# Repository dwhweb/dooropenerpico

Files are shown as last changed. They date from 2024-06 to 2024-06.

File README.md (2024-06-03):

Chicken 

# dooropenerpico

## Project overview

The purpose of this project is to create a door opener which can open and close the door to a chicken coop. It consists of —

- Python code written to run on a Raspberry Pi Pico W (hereafter referred to as the Pico).
- Various OpenSCAD models which can be customised and exported to .stl files for 3D printing.

The door can be toggled by pressing a button, and is integrated with Home Assistant as an MQTT entity and as such can be automated (for example, to open at sunrise). The microcontroller can also be optionally started with a web server for setup and debugging purposes by holding the button at startup.

On startup, the microcontroller will attempt to establish a connection to the wireless SSID specified within `/lib/dooropenerpico/credentials.conf`, then attempt to connect to the MQTT server also specified within that file. The onboard LED will blink to notify that this is happening, and will go solid when a connection is established. Following this, the green and red LEDs on the control panel will light in an alternating fashion twice to signify the board has successfully started. Most functions and actions the board takes are logged to the console for easy debugging in Thonny or your IDE of choice.

The door opener can operate without network functionality (button actuation only) by simply omitting `credentials.conf` if required.

## Documentation

Extensive documentation detailing how to build this project can be found [here](https://dwhweb.github.io/dooropenerpico).

## Licensing and acknowledgements

Unless otherwise noted for constituent parts, this project is shared under the terms of of the [CC-BY-4.0](https://creativecommons.org/licenses/by/4.0/) licence. Please attribute **dwhweb** in any derivative works.



The wiring diagram incorporates an .svg of the pinout of the Pico, which is the property of Raspberry Pi Ltd and is licenced under the terms of the [CC-BY-SA 4.0](https://creativecommons.org/licenses/by-sa/4.0/) licence, consequently the diagram is also shared under the terms of this licence.

The dooropenerpico project incorporates the following software, libraries and resources. If I've somehow missed you out, please get in touch —

- [Chicken image by Vecteezy](https://www.vecteezy.com/vector-art/6046486-chicken-logo-cartoon-character-cute-cartoon-rooster-chicken-gives-thumbs-up-vector-logo-illustrationt) (modified)
- The [Microdot](https://github.com/miguelgrinberg/microdot) library
- The [Picozero](https://github.com/RaspberryPiFoundation/picozero) library
- The [Public Domain Involute Parameterized Gears](https://www.thingiverse.com/thing:5505) library (modified to fix some minor issues)
- The [Umqtt.robust2](https://github.com/fizista/micropython-umqtt.robust2) library

The following software, libraries or resources were also used when creating this project —

- The [Belfry OpenSCAD library v2](https://github.com/BelfrySCAD/BOSL2)
- The [Furo theme](https://github.com/pradyunsg/furo)
- [Git](https://git-scm.com/)
- [Home Assistant](https://www.home-assistant.io/)
- [LunarVim](https://www.lunarvim.org/)
- [MicroPython](https://micropython.org/)
- [Mosquitto MQTT broker](https://mosquitto.org/)
- [MQTT Explorer](https://mqtt-explorer.com/)
- [OpenSCAD](https://openscad.org/)
- [PrusaSlicer](https://www.prusa3d.com/en/page/prusaslicer_424/)
- [Python](https://www.python.org/)
- [Rshell](https://github.com/dhylands/rshell)
- [Sphinx](https://www.sphinx-doc.org/en/master/)
- [Thonny](https://thonny.org/)
- The [Watchdog](https://github.com/gorakhargosh/watchdog) library

Thanks to the wider open source community for making projects like this possible and for creating fantastic things that we use every day.

## Contacts

Errors and omissions are likely and there are undoubtedly aspects of the project which are obvious to me but need clarification and improvement. You can contact me via email regarding this project at **dooropenerpico at dwhweb dot org**, or in the case of bugs raise a [Github issue](https://github.com/dwhweb/dooropenerpico/issues).

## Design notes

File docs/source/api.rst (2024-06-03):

API documentation
=================

.. toctree::

   class_structure

.. autosummary::
   :toctree: generated

   dooropenerpico.conf.Conf
   dooropenerpico.dooropenerpico.DoorOpenerPico
   dooropenerpico.dooropenerpicobase.DoorOpenerPicoBase
   dooropenerpico.dooropenerpiconetwork.DoorOpenerPicoNetwork
   dooropenerpico.dooropenerpicoweb.DoorOpenerPicoWeb
   dooropenerpico.print_debug.Print_debug

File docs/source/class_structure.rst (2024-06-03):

Class structure overview
========================

``main.py`` initially creates an instance of :class:`~dooropenerpico.dooropenerpico.DoorOpenerPico` which then instantiates one of three types of instance —

* :class:`~dooropenerpico.dooropenerpicobase.DoorOpenerPicoBase` (button functionality only) if ``credentials.conf`` (login credentials) or ``discovery.conf`` (Home Assistant discovery payload) can't be found.
* :class:`~dooropenerpico.dooropenerpicoweb.DoorOpenerPicoWeb` (web server) if the control panel button is held on startup.
* :class:`~dooropenerpico.dooropenerpiconetwork.DoorOpenerPicoNetwork` (Home Assistant/MQTT) otherwise.

These three classes have an inheritance relationship in terms of progressive enhancement as such —

.. inheritance-diagram:: dooropenerpico.dooropenerpicoweb
   :parts: 1

i.e. The majority of base functionality is implemented in :class:`~dooropenerpico.dooropenerpicobase.DoorOpenerPicoBase`, :class:`~dooropenerpico.dooropenerpiconetwork.DoorOpenerPicoNetwork` inherits from that and implements network/MQTT functionality, and :class:`~dooropenerpico.dooropenerpicoweb.DoorOpenerPicoWeb` inherits from that and implements web server functionality.

Aside from this, there are two utility classes —

* :class:`~dooropenerpico.conf.Conf` which is used to retrieve and validate ``.conf`` files.
* :class:`~dooropenerpico.print_debug.Print_debug` which is used to print debug messages to the console with an optional timestamp.

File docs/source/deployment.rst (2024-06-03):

.. include:: global.rst

Deployment and setup
====================

Cloning the repository
----------------------
Initially, clone the repository using Git —

.. code:: bash

   git clone https://www.github.com/dwhweb/dooropenerpico.git

Creating MQTT credentials
-------------------------
Assuming you plan on using the Home Assistant/MQTT broker functionality you'll need to create new user login credentials for the Pi Pico to use. You can find this option on Home Assistant in Settings → People → Users (Add user button) i.e. 

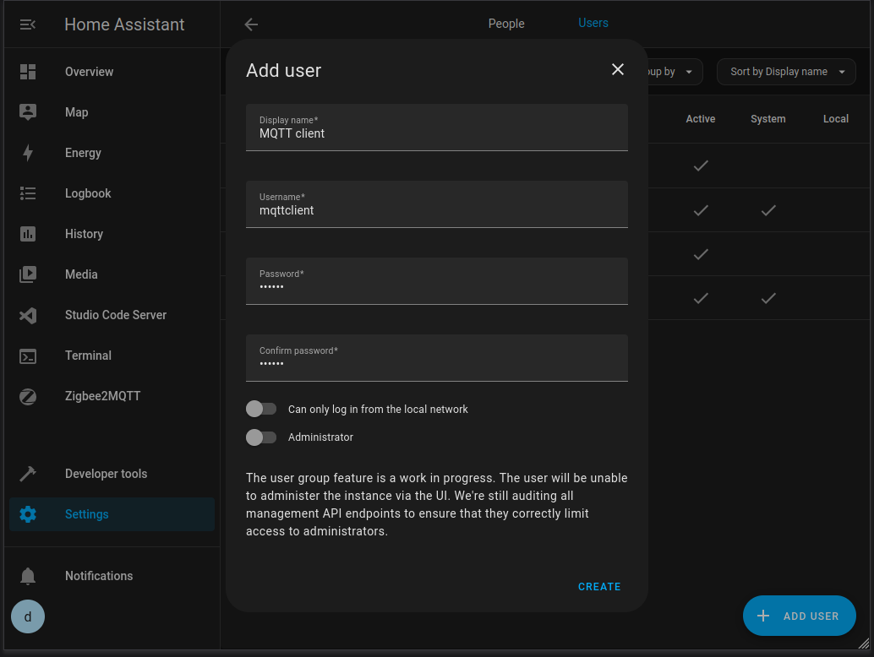
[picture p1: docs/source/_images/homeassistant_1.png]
Home Assistant users dialog


Once you've done that, you might want to verify that you can connect to the broker using MQTT explorer.
 
Deploying code to the Pi Pico
-----------------------------
Before you can copy the code across, you'll need to copy the MicroPython firmware to the Pico, follow the instructions on the `Raspberry Pi website. <https://www.raspberrypi.com/documentation/microcontrollers/micropython.html>`_

Deploying via script
^^^^^^^^^^^^^^^^^^^^
Once you have the MicroPython firmware installed, assuming you're running a \*nix variant you can deploy the code to the Pi Pico using ``deploy.sh`` (you need ``rshell`` for this to run, see the :doc:`software requirements <software>` section).

The script will inform you that the current contents of the Pi Pico will be erased, and ask if you want to set up networking. Assuming this is the case, you will be prompted for —

* Wifi SSID
* Wifi password
* MQTT broker hostname/IP
* MQTT port
* MQTT username
* MQTT password

Otherwise, the credentials file will be deleted and the Pico will operate via button press only (no networking) on boot.

.. note::

   The deployment script takes a little time to copy files across to the Pi Pico and provides little visual feedback while doing so, please be patient!

.. _deploying-manually:

Deploying manually
^^^^^^^^^^^^^^^^^^
If you're running Windows (or just don't want to run the script) and want to deploy the code to the Pi Pico manually, you need to copy ``main.py`` and the ``lib/`` directory across. You can do so using Thonny. With the Pi Pico connected, navigate to the directory where you cloned the code repository, then right click on the file/directory and select "Upload to /" i.e.

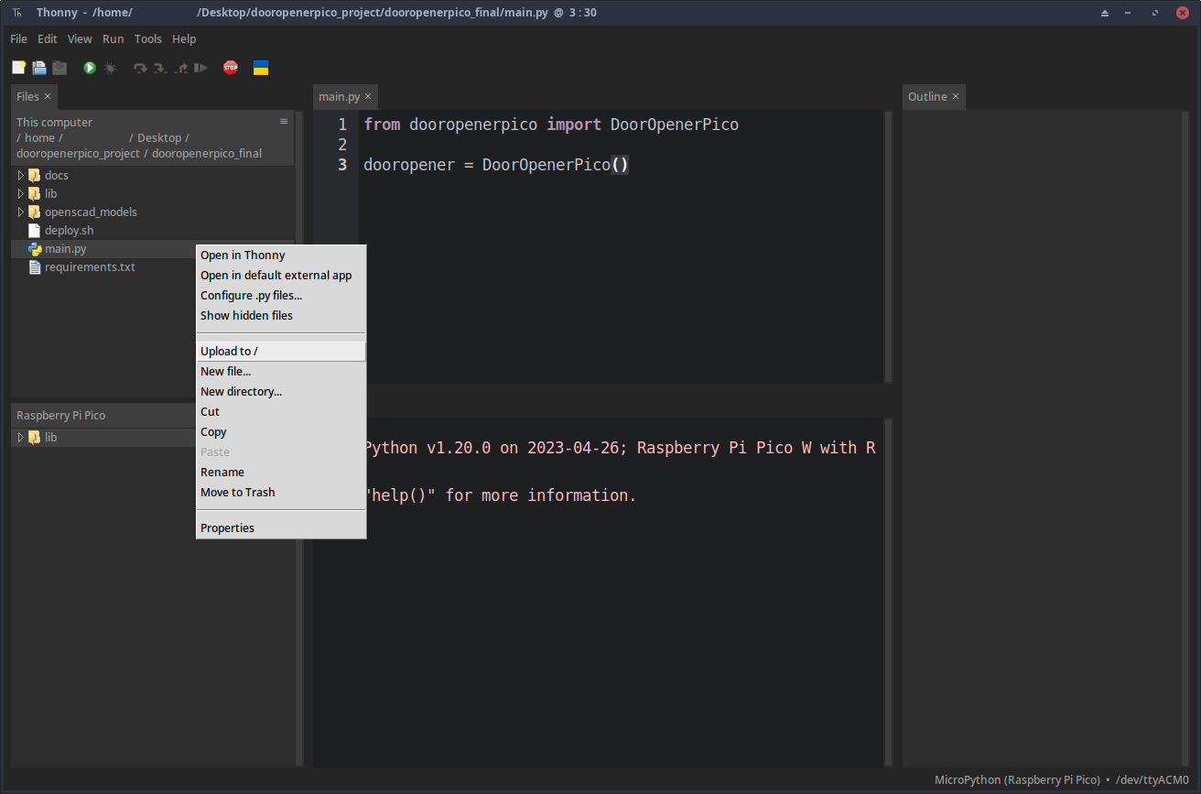
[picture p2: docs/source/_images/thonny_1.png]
Copying files to the Pi Pico


You can alternatively use ``rshell`` to copy the files with —

.. code:: bash

   cp main.py /pyboard/main.py
   cp -r lib/ /pyboard/

Once you've done that, you'll need to edit the credentials file ``/lib/dooropenerpico/credentials.conf`` to add Wifi/MQTT credentials as detailed above, or alternatively just delete the file if you don't plan to use network functionality.

.. _configuration-options:

Configuration options
---------------------

There are a number of configuration options held within ``/lib/dooropenerpico/config.conf`` that you might want to change, these are —

.. list-table::
   :header-rows: 1

   * - Key
     - Notes
   * - ``pulse_time``
     - The length of time the LEDs should pulse to indicate activity, in seconds.
   * - ``led_brightness``
     - Brightness of the LEDs when on, value is a float between 0-1.
   * - ``timeout``
     - The time in seconds after which the door opener aborts an open/close if the door doesn't detect it is in the opposite state, this is a safety feature. The web server provides a feature to time how long actuation takes which is useful in working out an appropriate value, see the :ref:`usage section <time-open-close>`.
   * - ``cushion_open_time``
     - Time after which the door changes speed when opening in seconds, the intention being that you could set the door to open more slowly for the last portion so it opens gently and does not slam. If you don't want this functionality, you can just set ``cushion_open_speed`` to be the same value as ``open_speed``. This must be less than ``timeout``, otherwise the door opener will not start. 
   * - ``cushion_close_time``
     - As above, but for the door closing as opposed to opening.
   * - ``open_speed``
     - The speed at which the door should open between 0 (full speed anti-clockwise) and 1 (full speed clockwise).
   * - ``close_speed``
     - As above, but for closing.
   * - ``cushion_open_speed``
     - The speed at which the door should open for the last (cushion) portion between 0 (full speed anti-clockwise) and 1 (full speed clockwise).
   * - ``cushion_close_speed``
     - As above, but for closing.
   * - ``left_reed_bounce_time``
     - Prevents activation of the left reed switch being detected as multiple events, value is in seconds.
   * - ``right_reed_bounce_time``
     - As above, but for the right reed switch.
   * - ``ping_interval``
     - Interval at which the Pi Pico should attempt to ping the MQTT broker, required to detect connection issues and re-establish connection automatically. If you encounter frequent connection issues it might be worth looking into getting an additional wireless access point or mesh setup.
   * - ``left_speed``
     - Speed at which the servo moves when the user presses the "left" button in the web ui, this is a float value between 0 and 1.
   * - ``right_speed``
     - As above, but for the "right" button.

You're most likely to need to tune the ``timeout`` and cushion times/speeds as it is likely that your coop is a different size than mine and hence the door will take a different amount of time to open or close. 

You'll likely need to tune ``left_speed`` and ``right_speed`` as well, even when using the same servo. There is a trim pot recessed into the side of the servo that you can set with a small phillips head screwdriver, this should be adjusted such that the servo doesn't move when stopped (you can send a stop signal from the web ui, see the :ref:`usage section <web-server>`). 

.. warning::

   Be careful when editing this file as it is validated on boot and if any key is missing or does not have an associated value the Pico won't start.

Setting up Home Assistant
-------------------------

I'm assuming at this point you have the Pico configured such that it successfully connects to both your Wifi and the Home Assistant MQTT broker, you can refer to the :ref:`usage section <console-output>` to see what the console output looks like in Thonny. 

Configuration in Home Assistant at this point should be relatively straightforward and the Pico should show in the list of entities (Settings → Devices & Services → Entities) —

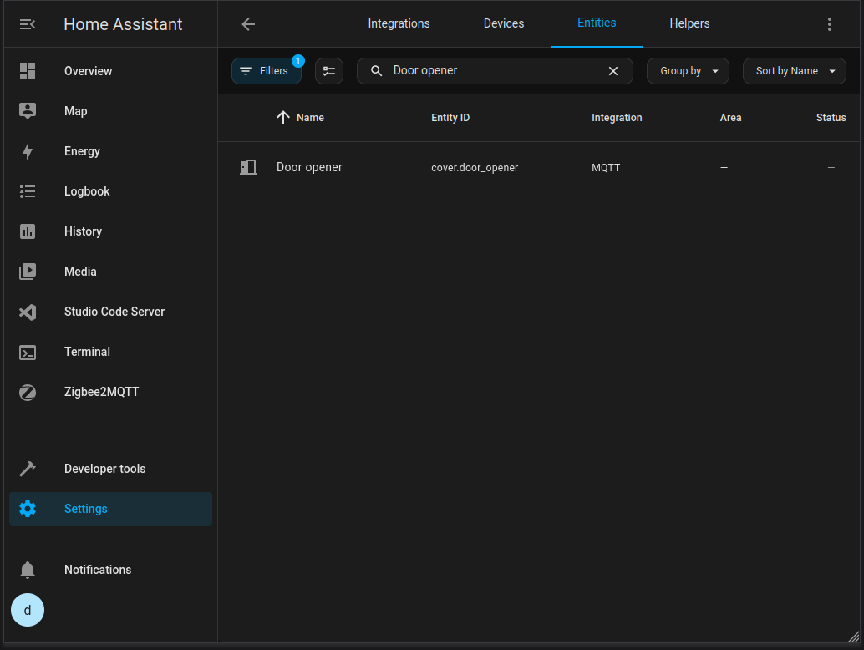
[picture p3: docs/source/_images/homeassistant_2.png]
The door opener entity


You can then add the door opener to the dashboard (Overview → Edit dashboard (pencil) icon → Add card → By entity) —

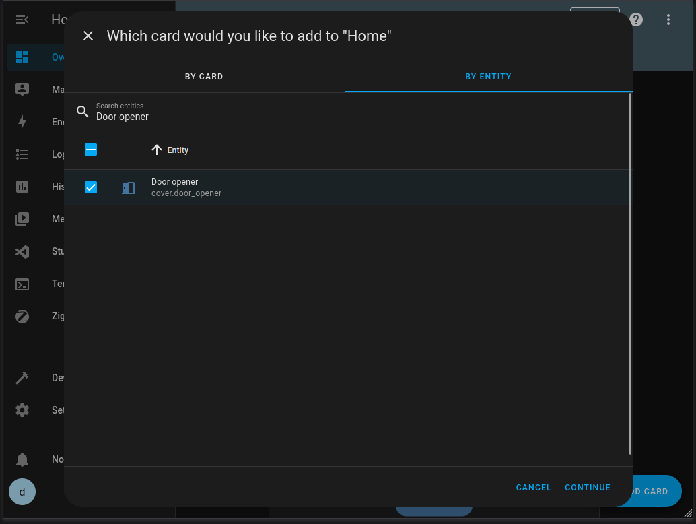
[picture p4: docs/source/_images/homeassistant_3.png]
Adding the door opener to the dashboard


You could then create an automation, for example, to open the door automatically at sunrise (Settings → Automations & scenes → Create automation) —

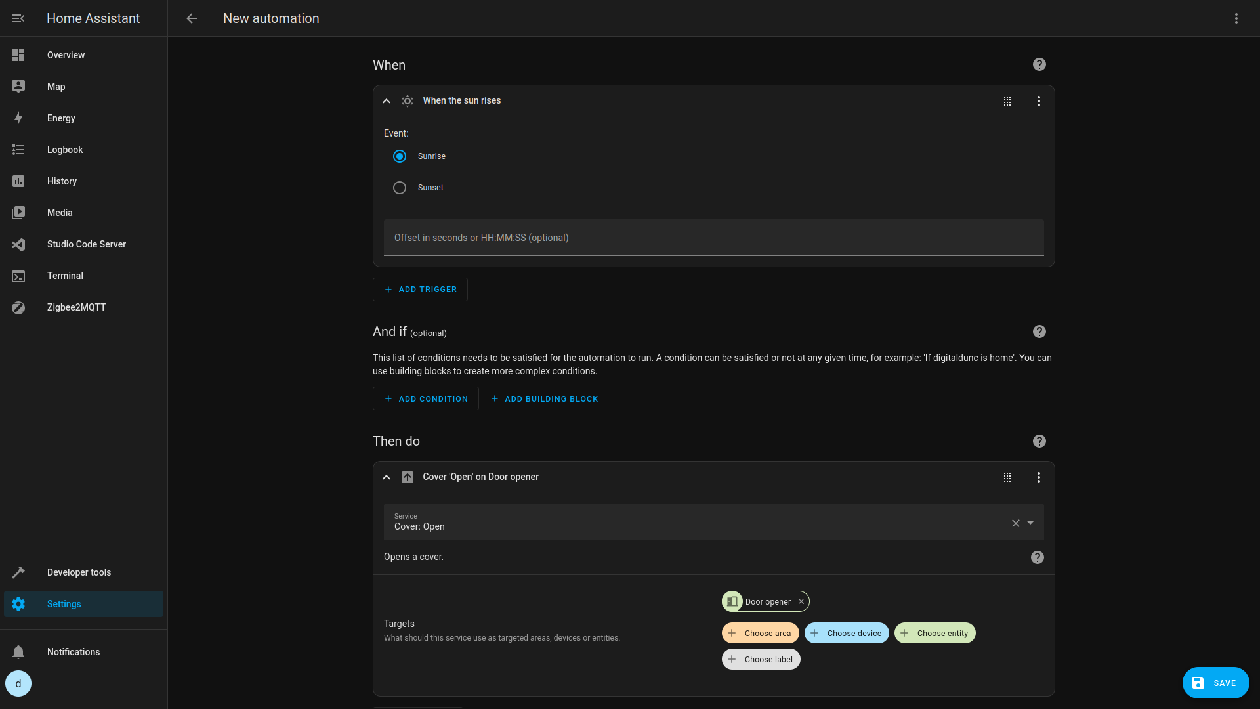
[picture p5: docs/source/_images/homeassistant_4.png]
Door opener automation


I don't personally automate closing the door, as the time at which my chickens decide to go in varies and I don't want them to accidentally get trapped in the door.

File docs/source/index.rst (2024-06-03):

.. include:: global.rst

.. toctree::
   :hidden:
   :maxdepth: 5
   
   Project overview <self>
   video
   skills
   software
   bom
   printing
   wiring
   deployment
   usage
   troubleshooting
   development
   api
   licencing
   contacts

dooropenerpico documentation
============================

Project overview
----------------

The purpose of this project is to create a door opener which can open and close the door to a chicken coop. It consists of —

- Python code written to run on a Raspberry Pi Pico W (hereafter referred to as the Pico).
- Various OpenSCAD models which can be customised and exported to .stl files for 3D printing.

The door can be toggled by pressing a button, and is integrated with `Home Assistant <https://www.home-assistant.io>`_ as an MQTT entity and as such can be automated (for example, to open at sunrise). The microcontroller can also be optionally started with a web server for setup and debugging purposes by holding the button at startup.

On startup, the microcontroller will attempt to establish a connection to the wireless SSID specified within ``/lib/dooropenerpico/credentials.conf``, then attempt to connect to the MQTT server also specified within that file. The onboard LED will blink to notify that this is happening, and will go solid when a connection is established. Following this, the green and red LEDs on the control panel will light in an alternating fashion twice to signify the board has successfully started. Most functions and actions the board takes are logged to the console for easy debugging in Thonny or your IDE of choice.

The door opener can operate without network functionality (button actuation only) by simply omitting ``credentials.conf`` if required.

The files for this project in terms of MicroPython code and OpenSCAD models can be found in the repository on `Github <https://www.github.com/dwhweb/dooropenerpico>`_.

.. note:: 
   I built this project for my own personal use and as such it is likely not suited to your purposes without some minor customisation, but the code and models were created with this in mind and this is covered in more depth in the sections to follow. 

.. tip::
   If you intend on building the project, I suggest you scan the documentation in its entirety before you start so you have a better appreciation of how the various parts (hardware and software) fit together.

.. warning::
   In case it isn't obvious, no warranty is expressed or implied. I am not responsible for any harm that might come to you, your chickens, the fabric of spacetime, etc.

|CC BY 4.0|

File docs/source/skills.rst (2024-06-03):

Required skills
================

I'd suggest that you have the following skills to proceed with this project —

* Familiarity with your operating system of choice, and some technical level of computing experience. 
  
  * Most of the things you'll need to do in the course of building this project can *probably* be done in Windows, but a shell script for code deployment to the Pico is included in the repository so Linux is probably preferable.
  * You'll need some kind of Home Assistance instance to get the most out of this project in terms of automation so familiarity with virtualisation could be beneficial if you want to run it in a VM or container.
* Rudimentary experience of electronics, and the ability to solder. You'll need to wire together some of the components in the BOM (Bill Of Materials).
* Some coding experience in general (especially object-oriented Python) would be beneficial, but coding on your part should be largely unnecessary — important configurables are held within ``.conf`` files.
* Familiarity with OpenSCAD would be beneficial but again, necessary changes on your part should be minimal and important configurables can be changed directly within the OpenSCAD UI.
* 3D printing experience, you should be familiar with standard concepts such as slicing, fill percentages, supports and the properties of different printing materials.

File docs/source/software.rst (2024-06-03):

Software requirements
=====================

I'd suggest the following software if you intend to build this project —

* `Git <https://git-scm.com/>`_ to clone the repository ready for deployment.
* Linux or some flavour of \*nix for running the code deployment Bash script for copying the microcontroller code to the Pi Pico — you can alternatively :ref:`deploy this manually <deploying-manually>`.
* `rshell <https://github.com/dhylands/rshell>`_ if you're using the code deployment script.
* `Thonny <https://thonny.org/>`_ as an IDE — even if you aren't likely to change any of the underlying code the console is invaluable for debugging purposes and Thonny also sets the RTC of the Pico on connection so you can determine *when* an issue happened.
* `OpenSCAD <https://openscad.org/>`_ for customising and exporting the 3D models ready for printing.
* `The Belfry OpenSCAD library v2 <https://github.com/BelfrySCAD/BOSL2>`_ is a required library for the 3D models.
* `PrusaSlicer <https://www.prusa3d.com/en/page/prusaslicer_424/>`_ is my preferred slicer, but Cura or similar would work just as well.
* `Home Assistant <https://www.home-assistant.io/>`_ for automating when the door opens or closes, if you don't care about network functionality and just want to use the switch you can omit this.
* `Mosquitto MQTT broker <https://mosquitto.org/>`_ installed as a Home Assistant add-on, you may already have this depending on what is running on your Home Assistant instance.
* `MQTT Explorer <https://mqtt-explorer.com/>`_ is useful for debugging MQTT issues.

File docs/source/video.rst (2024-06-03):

Video and images
================

Video
-----
Video of the door opener actuating —

..  youtube:: s7rDaMlY8wI

Fully assembled
---------------
The opener looks like this when assembled —

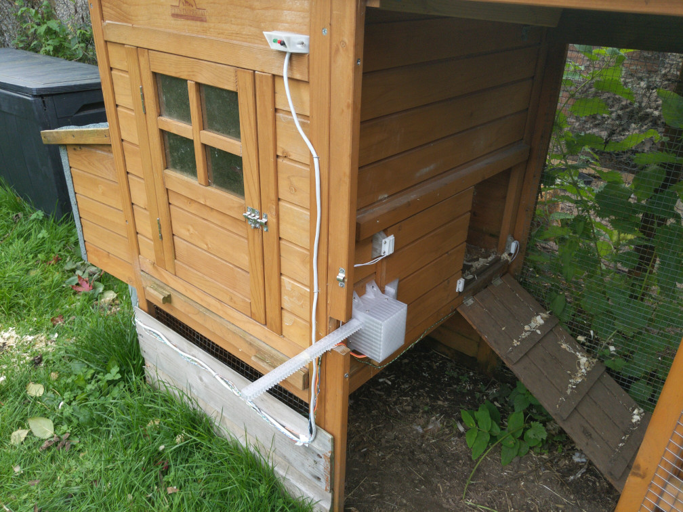
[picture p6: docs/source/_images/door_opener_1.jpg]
Assembled door opener


Pico case
---------
The casing for the Pico is out of shot in a plastic box underneath the coop which also holds a mains supply. The case for the Pico without the cover looks like this —

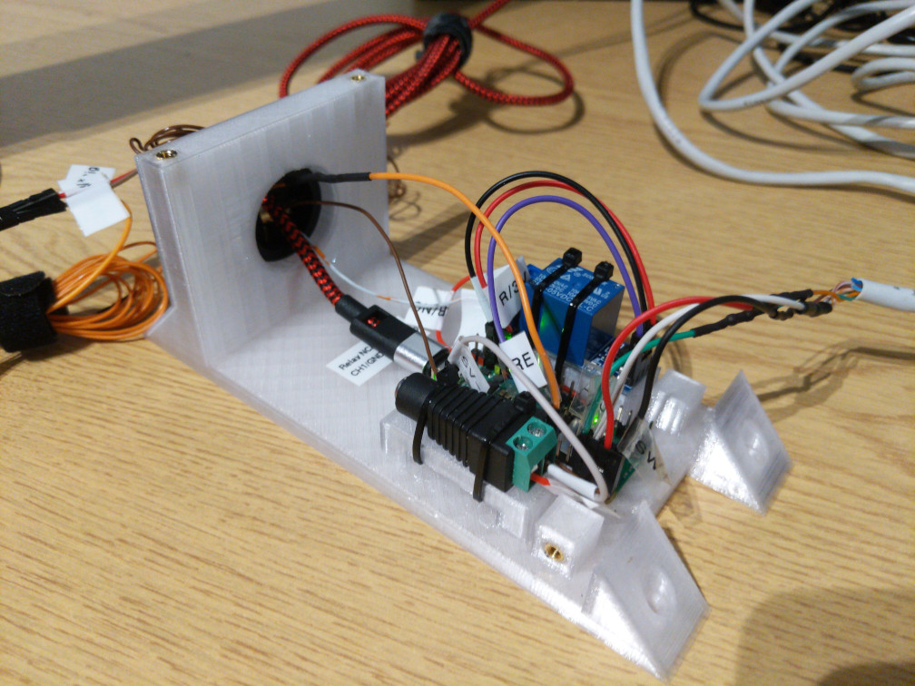
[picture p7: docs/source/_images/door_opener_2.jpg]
Pi pico case without cover


Note that the project is only partially assembled in the above picture and not all cables are shown. Fully assembled, the case looks like this —

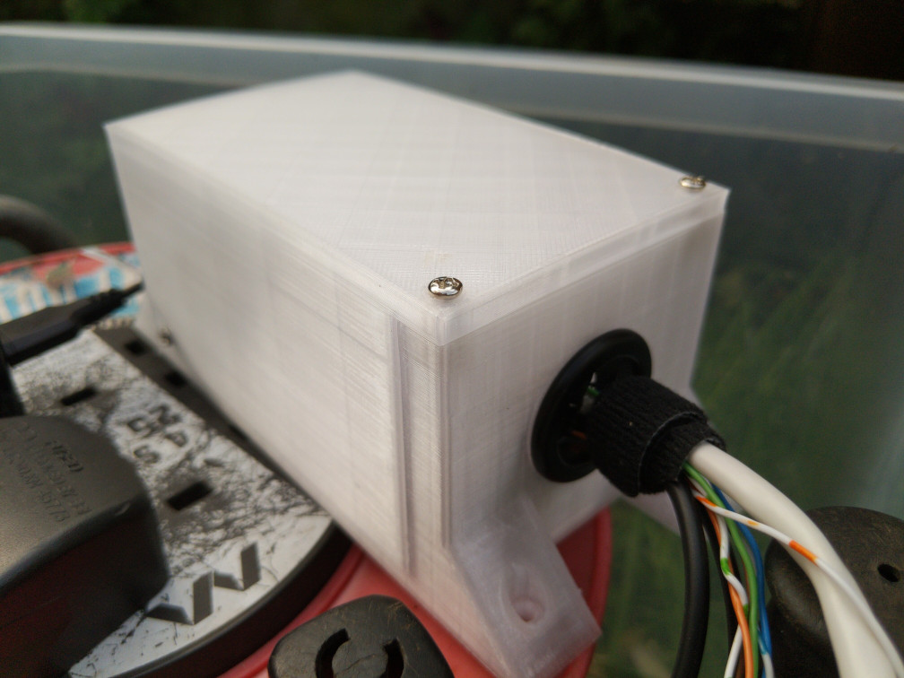
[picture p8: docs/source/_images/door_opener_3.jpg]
Pi pico case with cover


Control panel
-------------
The control panel looks like this —

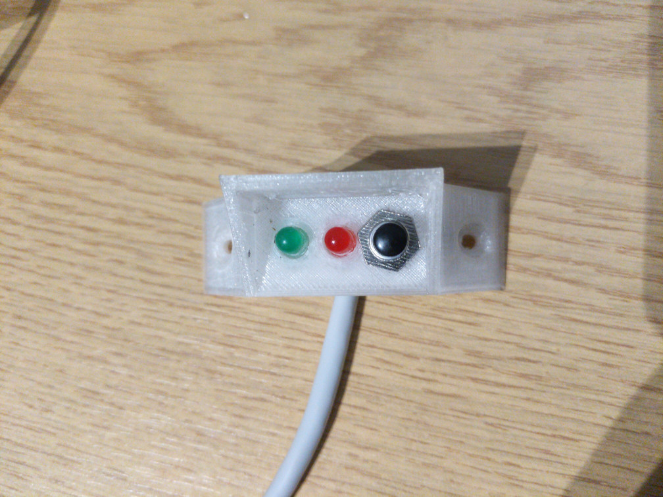
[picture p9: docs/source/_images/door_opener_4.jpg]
Control panel


Reed switch mounts
------------------
Left and right reed switch mounts (respectively) look like this —

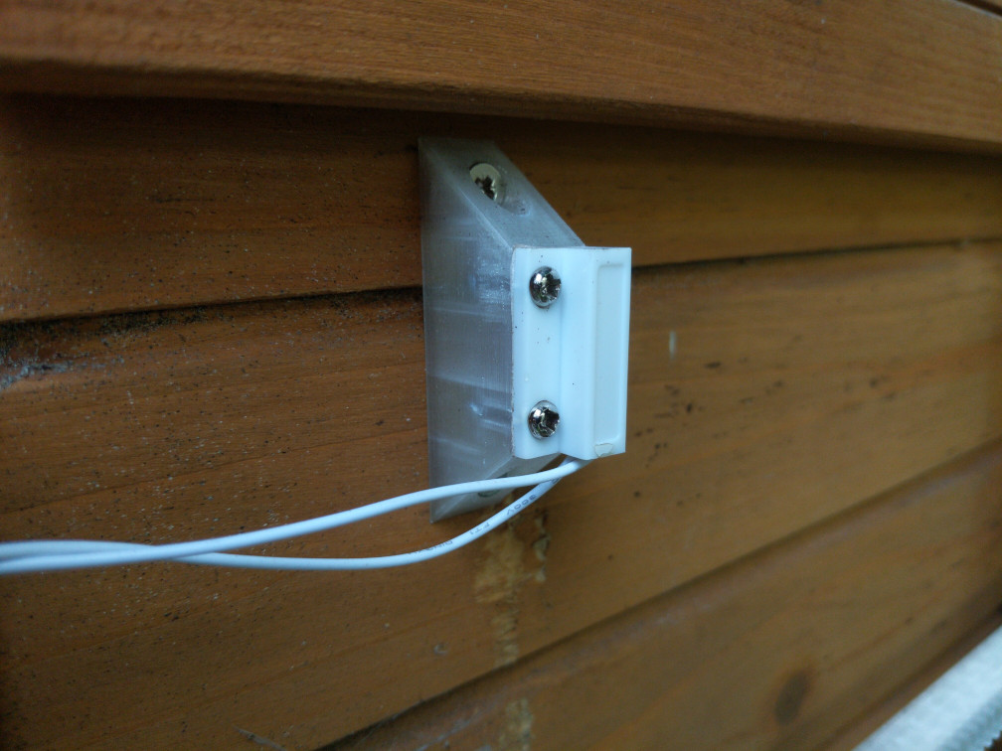
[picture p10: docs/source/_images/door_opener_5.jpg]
Left reed switch mount


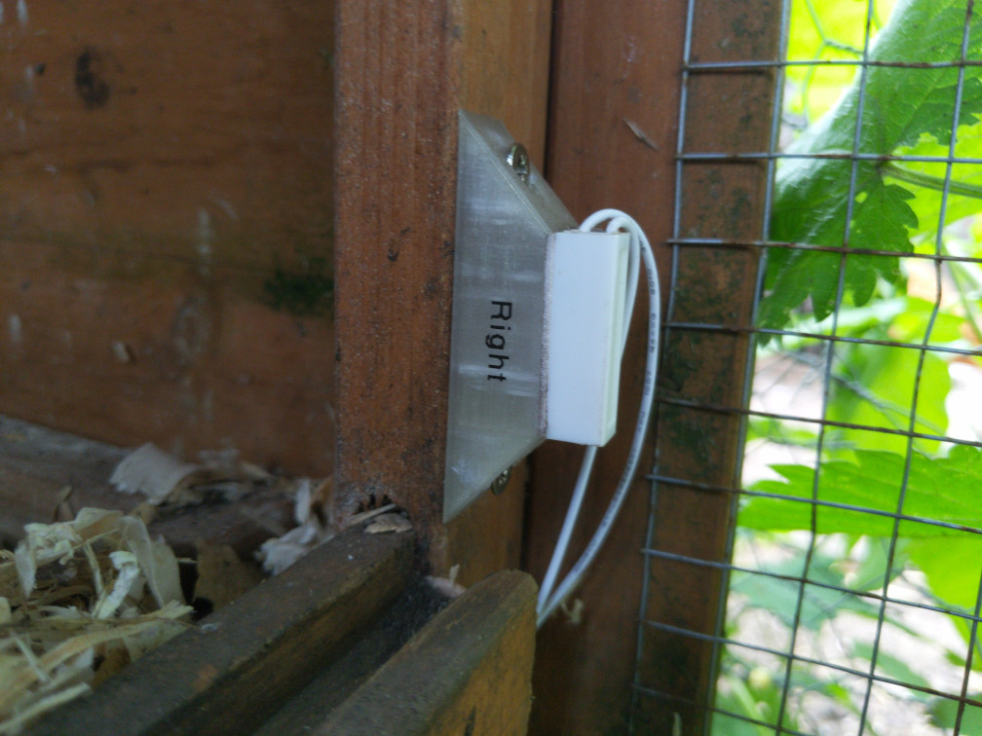
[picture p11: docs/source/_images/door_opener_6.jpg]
Right reed switch mount


Servo rack
----------
The servo rack as mounted to the door looks like this —

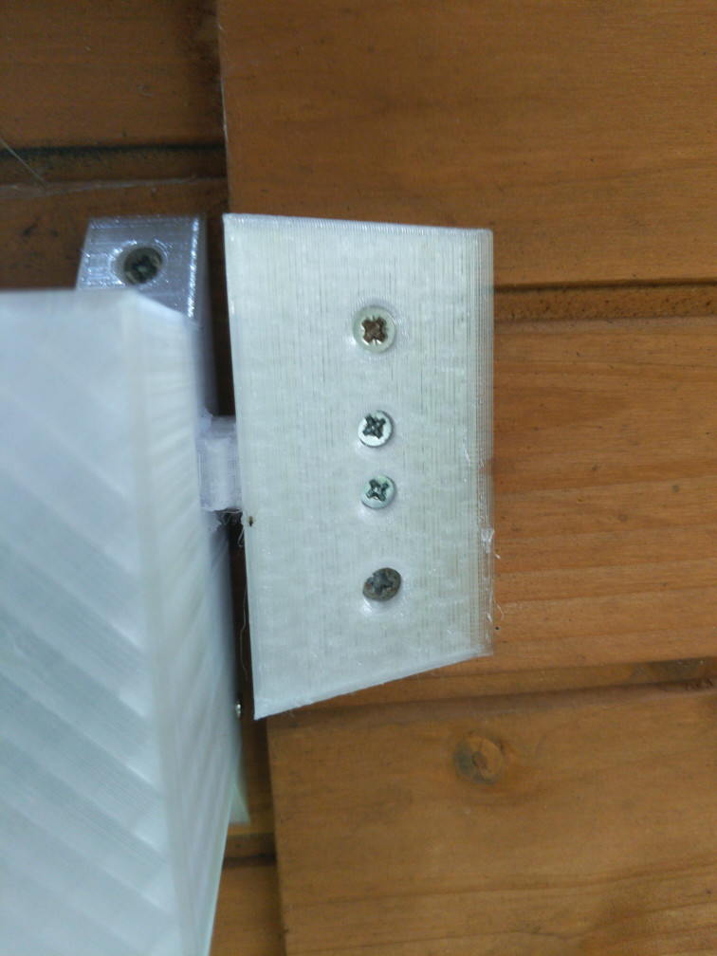
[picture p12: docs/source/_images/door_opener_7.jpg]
Door opening rod


Door opener
-----------
The servo as mounted in the door opener base looks like this —

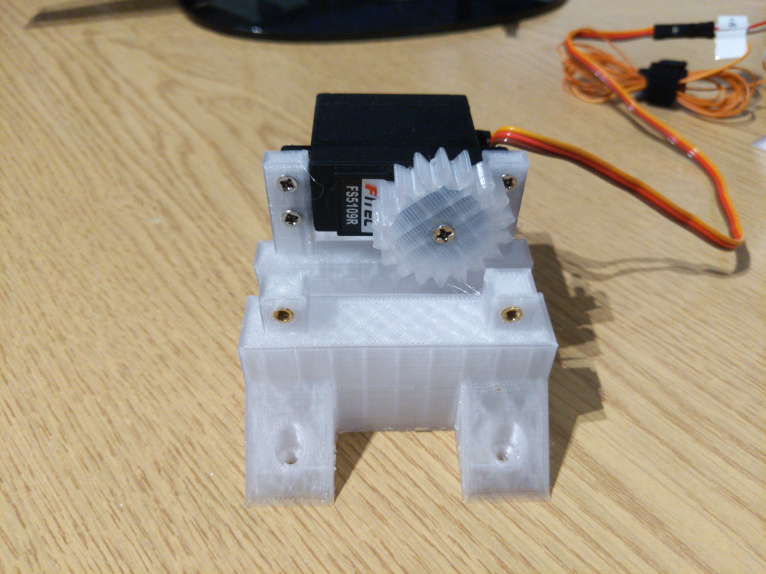
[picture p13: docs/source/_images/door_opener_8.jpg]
Servo mounted in base


And fully assembled —

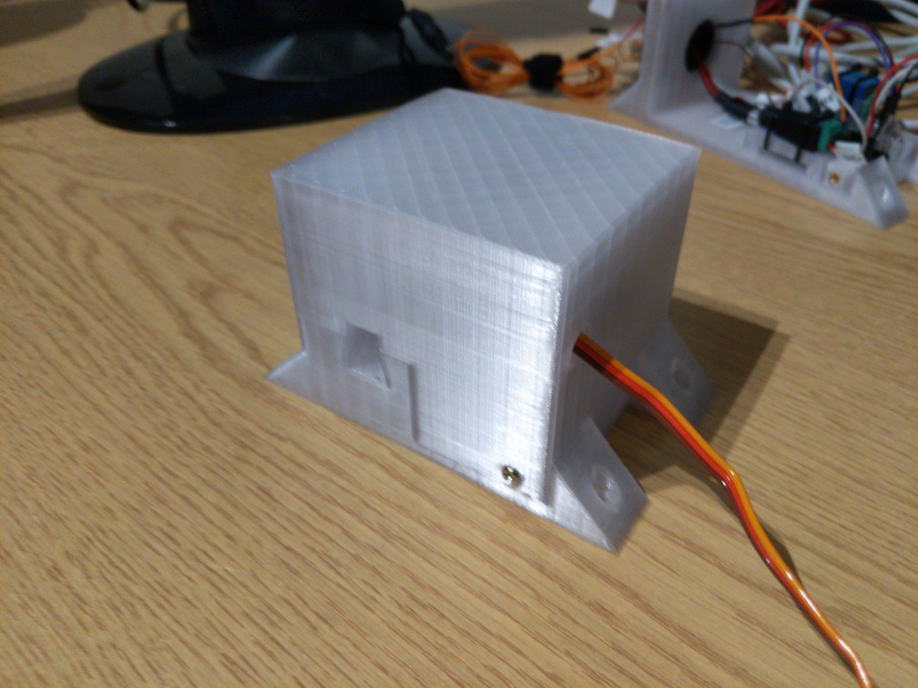
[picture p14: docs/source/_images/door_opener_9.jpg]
Door opener fully assembled


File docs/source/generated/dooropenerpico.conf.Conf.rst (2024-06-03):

Conf
====

.. currentmodule:: dooropenerpico.conf

.. autoclass:: Conf

   .. automethod:: __init__

   .. rubric:: Methods

   .. autosummary::
   
      ~Conf.__init__

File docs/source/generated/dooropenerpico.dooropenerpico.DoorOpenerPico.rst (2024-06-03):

DoorOpenerPico
==============

.. currentmodule:: dooropenerpico.dooropenerpico

.. autoclass:: DoorOpenerPico

   .. automethod:: __init__

   .. rubric:: Methods

   .. autosummary::
   
      ~DoorOpenerPico.__init__

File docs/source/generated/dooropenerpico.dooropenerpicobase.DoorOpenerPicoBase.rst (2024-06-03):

DoorOpenerPicoBase
==================

.. currentmodule:: dooropenerpico.dooropenerpicobase

.. autoclass:: DoorOpenerPicoBase

   .. automethod:: __init__

   .. rubric:: Methods

   .. autosummary::
   
      ~DoorOpenerPicoBase.__init__

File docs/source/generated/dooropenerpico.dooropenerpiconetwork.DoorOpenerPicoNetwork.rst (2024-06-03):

DoorOpenerPicoNetwork
=====================

.. currentmodule:: dooropenerpico.dooropenerpiconetwork

.. autoclass:: DoorOpenerPicoNetwork

   .. automethod:: __init__

   .. rubric:: Methods

   .. autosummary::
   
      ~DoorOpenerPicoNetwork.__init__

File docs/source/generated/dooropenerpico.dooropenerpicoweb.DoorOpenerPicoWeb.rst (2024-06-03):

DoorOpenerPicoWeb
=================

.. currentmodule:: dooropenerpico.dooropenerpicoweb

.. autoclass:: DoorOpenerPicoWeb

   .. automethod:: __init__

   .. rubric:: Methods

   .. autosummary::
   
      ~DoorOpenerPicoWeb.__init__

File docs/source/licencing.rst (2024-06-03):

.. include:: global.rst

Licencing and acknowledgements
==============================

Unless otherwise noted for constituent parts, this project is shared under the terms of of the `CC-BY-4.0 <https://creativecommons.org/licenses/by/4.0/>`_ licence. Please attribute **dwhweb** in any derivative works.

|CC BY 4.0|

The wiring diagram incorporates an .svg of the pinout of the Pico, which is the property of Raspberry Pi Ltd and is licenced under the terms of the `CC-BY-SA 4.0 <https://creativecommons.org/licenses/by-sa/4.0/>`_ licence, consequently the diagram is also shared under the terms of this licence.

The dooropenerpico project incorporates the following software, libraries and resources. If I've somehow missed you out, please get in touch —

* `Chicken image by Vecteezy <https://www.vecteezy.com/vector-art/6046486-chicken-logo-cartoon-character-cute-cartoon-rooster-chicken-gives-thumbs-up-vector-logo-illustrationt>`_ (modified)
* The `Microdot <https://github.com/miguelgrinberg/microdot>`_ library
* The `Picozero <https://github.com/RaspberryPiFoundation/picozero>`_ library
* The `Public Domain Involute Parameterized Gears <https://www.thingiverse.com/thing:5505>`_ library (modified to fix some minor issues)
* The `Umqtt.robust2 <https://github.com/fizista/micropython-umqtt.robust2>`_ library

The following software, libraries or resources were also used when creating this project —

* The `Belfry OpenSCAD library v2 <https://github.com/BelfrySCAD/BOSL2>`_
* The `Furo theme <https://github.com/pradyunsg/furo>`_
* `Git <https://git-scm.com/>`_
* `Home Assistant <https://www.home-assistant.io/>`_
* `LunarVim <https://www.lunarvim.org/>`_
* `MicroPython <https://micropython.org/>`_
* `Mosquitto MQTT broker <https://mosquitto.org/>`_
* `MQTT Explorer <https://mqtt-explorer.com/>`_
* `OpenSCAD <https://openscad.org/>`_
* `PrusaSlicer <https://www.prusa3d.com/en/page/prusaslicer_424/>`_
* `Python <https://www.python.org/>`_
* `Rshell <https://github.com/dhylands/rshell>`_
* `Sphinx <https://www.sphinx-doc.org/en/master/>`_
* `Thonny <https://thonny.org/>`_
* The `Watchdog <https://github.com/gorakhargosh/watchdog>`_ library

Thanks to the wider open source community for making projects like this possible and for creating fantastic things that we use every day.

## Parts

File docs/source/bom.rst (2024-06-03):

Bill of materials
-----------------

General suggestions
^^^^^^^^^^^^^^^^^^^

* I'm assuming you have basic soldering and electronics equipment like a soldering iron, solder, flux, multimeter, side cutters, wire strippers and so on.
* A laptop is pretty much essential to customise and debug the Pico when it is mounted.
* I have a mains extension reel, DC adapters and the Pico case in a plastic box with suitable holes for cable ingress to protect everything from the elements, you'll likely need something similar. 
* For the sake of expediency I'd suggest you pick up a set of assorted M2 and M3 screws and a few bags of mixed dupont jumper cables with both male and female ends. 
* I used the individual wires within Cat5 network cable for splicing purposes as I have a lot of that spare, but I've suggested wires of the correct colours, which would be nicer. Obviously any low gauge copper wire would be suitable.
* Making small labels for the wires with a label printer makes things a lot easier, if you happen to have one.
* As you're likely to be doing a fair amount of splicing, assorted sizes of heatshrink will keep your connections tidy.
* You'll need approximately 357g of filament in total — you can likely get away with printing most of the project in PLA if you really want to, but I'd suggest you print at least the servo gear and servo rack in PETG due to the better tensile strength of that material.
* It's worth checking out whether you have sufficient wireless coverage with your router/access point to communicate reliably with the Pico. I had to buy an additional access point and set up a wireless mesh but this is obviously dependent on where your Pico is located.
* The vast majority of these parts were sourced from Ebay, but you'll likely find the parts relatively easily from the usual Chinese retailers like Aliexpress.
* Some of the choices of parts (such as imperial screws and the cable grommet) aren't necessarily the best choices and were only used because I had them to hand — feel free to substitute if you have something better that you think will work.

Door opener
^^^^^^^^^^^

.. list-table::
   :header-rows: 1

   * - Item
     - Quantity
     - Notes
   * - PETG filament
     - 125g
     - You'll need approximately 125g of filament for the door opener base and cover at 15% infill.
   * - M3 brass screw inserts
     - 4
     - These should be inserted into the holes at the front and back of the door opener with a soldering iron.
   * - M3x12 screw (countersunk)
     - 4
     - Attaches the servo to the case posts.
   * - M3x10 screw (flat head)
     - 4
     - Attaches the cover to the base.
   * - M3 nuts
     - 4
     - For attaching the servo to the case posts.
   * - 6 x ½ screw (imperial)
     - 4
     - For mounting the door opener to the coop. I used these because I had them lying around, use the closest metric equivalent (3x12mm) if you can't find them.
   * - Brown/red/orange dupont cable (male)
     - 3
     - For connecting to the servo, it doesn't really matter what sex the other end is as you'll be cutting and splicing with other cables.
   * - Orange dupont cable (female)
     - 1
     - Servo PWM signal wire, connects to the Pico, this should be spliced to the orange male dupont wire (you'll likely have a longer section of wire spliced between the two)
   * - Orange copper wire
     - 1
     - Splice between the orange male and female dupont cables.
   * - Brown copper wire
     - 1
     - Solder to the brown male dupont cable (Servo -) and connect the other end to the negative screw terminal of the DC connector.
   * - Red copper wire
     - 1
     - Solder to the red male dupont cable (Servo +) and connect the other end to the COM (Common) screw terminal of the relay.
   * - Silicone grease (optional)
     - 1
     - Use for lubricating the channel the opening rod is in for easier actuation.
   * - Feetech FS5109R continuous rotation servo
     - 1
     - Most full size RC car servos use a similar form factor, so you might be able to use something else if you can't find this specific servo. The important things are that the servo is continuous rotation, can supply enough torque for the weight of your door and has a metal hub and gears. Cheaper plastic versions will get mashed up pretty quickly.

Raspberry Pi Pico case
^^^^^^^^^^^^^^^^^^^^^^

.. list-table::
   :header-rows: 1

   * - Item
     - Quantity
     - Notes
   * - PETG filament
     - 147g
     - You'll need approximately 147g of filament at 15% infill, including supports under the raised portions where the female DC connector and relay portions are attached to the case.
   * - Raspberry Pi Pico W
     - 1
     - N/A
   * - 20 pin header
     - 2
     - For the Pico, the colour coded versions that the Pi hut supplies are nice. You could alternatively get a board with the headers pre-soldered.
   * - M2 brass screw inserts
     - 4
     - Insert these into the holes in the base with a soldering iron.
   * - M2 x 6 screw, flat head
     - 4
     - Attaches the Pico to the centre of the case.
   * - M3 brass screw inserts
     - 4
     - Insert these into the holes in the top of the wall on the base and the holes on the sides of the small posts at the front of the base with a soldering iron.
   * - M3 x 10 screw, flat head
     - 4
     - For attaching the cover to the base.
   * - Small cable ties
     - 4
     - For attaching the DC connector and relay to the raised sections in the bottom of the case, these need to be fairly thin for the cover to fit on properly.
   * - 5.5 x 2.5mm right angled male to female DC extension cable
     - 1
     - For attaching internally to the DC connector, potentially optional if the connector on the end of your DC adapter fits inside the case.
   * - 5.5 x 2.5mm 6V 4A DC adapter
     - 1
     - For powering the servo, stall current for the FS5109R is around 2A at 6V but the servo accepts a range of voltages so you'd probably be fine with a more common 5V adapter.
   * - 5.5 x 2.5mm female DC connector with screw terminals
     - 1
     - Connects to the relay, servo - and Pico ground.
   * - 3.3V/5V 10A Relay Module
     - 1
     - Completely isolates the power supply from the servo when deactivated, 5V versions of the relay are quite common but you need to ensure you get a version that can use the 3.3v output from the Pico.
   * - Micro USB cable, 1m
     - 1
     - For powering/debugging the Pico.
   * - 5V DC USB AC adapter
     - 1
     - The Pico sips power, so any 5V adapter will likely work. You could potentially power the Pico from the 6V DC adapter with a suitable buck converter or similar, but I've kept it separate for easy code debugging.
   * - 30mm cable grommet
     - 1
     - For the hole the cables enter the case through. The one I used I had lying around, and I'm unsure if commercially available ones are exactly the same dimensions in terms of lip size so you might need to adjust this in the OpenSCAD model.
   * - Purple dupont cable (Female)
     - 1
     - For the relay signal connection.
   * - Black dupont cable (Female)
     - 2
     - For the relay ground, the other should be used for connecting the - side of the DC connector to a ground on the Pico.
   * - Red dupont cable (Female)
     - 1
     - For the relay 3v supply.
   * - Red copper wire
     - 1
     - Connects the + side of the DC connector to the NO connector on the relay.

Reed switch mounts
^^^^^^^^^^^^^^^^^^

.. list-table::
   :header-rows: 1

   * - Item
     - Quantity
     - Notes
   * - PETG filament
     - 12g
     - You'll need approximately 12g of filament at 15% infill.
   * - 6 x ½ screw (imperial)
     - 4
     - For fixing the reed switch mounting blocks to the coop.
   * - 2.5 x 10mm screw, flat head
     - 8
     - In my case these came with the reed switches, hopefully you shouldn't need to buy them. For fixing the reed switches to the mounting blocks, and their matching magnets to the door.
   * - MC-38 wired magnetic door/window sensor
     - 2
     - The reed switch and magnet pairs, one pair for the left position (open) and one for the right position (closed).
   * - Black dupont cable (female)
     - 2
     - For the ground side of the reed switches.
   * - White dupont cable (female)
     - 2
     - For the positive side of the reed switches.
   * - Black copper wire
     - 2
     - For splicing between the ground side of the reed switches and the black dupont cables.
   * - White copper wire
     - 2
     - For splicing between the positive side of the reed switches and the white dupont cables.

Servo gear
^^^^^^^^^^

.. list-table::
   :header-rows: 1

   * - Item
     - Quantity
     - Notes
   * - PETG filament
     - 5g
     - You'll need approximately 5g of filament at 15% infill.
   * - 20mm diameter 25T circular aluminium servo horn
     - 1
     - You'll probably get a plastic version with your servo but you need a metal horn due to the forces involved.
   * - Two part epoxy
     - 1
     - For gluing the servo horn into the centre of the servo gear, you could alternatively use superglue or any adhesive you trust to attach plastic to aluminium.
   * - M3x8 screw (countersunk)
     - 1
     - For attaching the servo gear to the hub of the servo, if you have a screw supplied with your servo that might be suitable.

Servo rack
^^^^^^^^^^

.. list-table::
   :header-rows: 1

   * - Item
     - Quantity
     - Notes
   * - PETG filament
     - 54g
     - I'd suggest you use a higher infill for the rack, as that is where the majority of force is applied. For a 310mm rack (default, bracket not included) at 25% infill you'll need approximately 54g.
   * - 6 x ½ screw (imperial)
     - 2
     - For mounting the rack bracket to the door, the two outer holes in the bracket.
   * - 2.5 x 16mm Screw (metric, optional)
     - 2
     - These are for the two centre holes on the opening rod, they came with my coop and the holes on the rack line up with existing holes on my door for the original manual opening rod. As you're unlikely to have the same screws, the OpenSCAD model has an option to use all 6x½ holes instead if you'd prefer.
   * - Two part epoxy
     - 1
     - The rack is so long as to be printed in two parts and joined together; the epoxy is for gluing together at the dovetail joint where the two pieces join.
   * - Sandpaper
     - 1
     - When the two parts of the rack are glued together you'll likely find that they aren't totally level and hitch at the join when moving in the door opener channel. You should sand the join to ensure the rack moves freely.

Switch panel
^^^^^^^^^^^^

.. list-table::
   :header-rows: 1

   * - Item
     - Quantity
     - Notes
   * - PETG filament
     - 14g
     - You'll need approximately 14g of filament at 15% infill with supports.
   * - Red 5mm LED
     - 1
     - N/A
   * - Green 5mm LED
     - 1
     - N/A
   * - 7mm momentary SPST switch
     - 1
     - N/A
   * - 330Ω resistor
     - 2
     - For the LEDs.
   * - Cat5 patch cable
     - 1
     - I used a single patch cable as a way of keeping cabling to the switch panel neat, you can use single wires for the red LED +, green LED + and switch + and tie all the ground wires together for connection to a single pin on the Pico.
   * - Red dupont cable (female)
     - 1
     - For the red LED.
   * - Green dupont cable (female)
     - 1
     - For the green LED
   * - White dupont cable (female)
     - 1
     - For the switch +
   * - Black dupont cable (female)
     - 1
     - For the common ground (red LED, green LED and switch)
   * - Two part epoxy
     - 1
     - For gluing the red and green LEDs in place.
   * - Cable staples
     - 12
     - For securing the patch cable and any other cables to the coop.

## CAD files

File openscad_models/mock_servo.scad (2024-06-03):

$fn = 50;

module mock_servo() {
  mock_servo = [40, 38, 19.5];
  bracket = [7, 2.5, 19.5];

  translate([0, -bracket.y, 0]) bracket(bracket); // Left bracket
  translate([(bracket.x * 2) + mock_servo.x, -bracket.y, 0]) mirror([1, 0, 0]) bracket(bracket); // Right bracket
  translate([bracket.x, 6, 0]) { // 6mm from front to bracket
    translate([0, -mock_servo.y, 0]) cube(mock_servo);
    color("white") translate([10, 0, mock_servo.z / 2]) rotate([-90, 0, 0]) cylinder(h=8, d=5.3); // Horn mount
  }
}

module bracket(bracket) {
  line = [7, 1.6, 1];
  hole_diameter = 4;

    difference() {
      cube(bracket); // Main body
      translate([bracket.x / 4, bracket.y + 1, (bracket.z / 4) * 3]) rotate([90, 0, 0]) cylinder(h=bracket.y + 2, d=hole_diameter); // Top hole
      translate([bracket.x / 4, bracket.y + 1, bracket.z / 4]) rotate([90, 0, 0]) cylinder(h=bracket.y + 2, d=hole_diameter); // Bottom hole
    }

    translate([0, bracket.y, (bracket.z / 2) - (line.z / 2)]) cube(line); // Raised line
}

mock_servo();

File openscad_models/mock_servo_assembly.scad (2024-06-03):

use <servo_gear.scad>
use <mock_servo_horn.scad>
use <mock_servo.scad>

$fn = 50;

module mock_servo_assembly() {
  bracket_spacing = 6; // Space between the edge of the main body of the servo and the bracket
  horn_mount_height = 8; // Height of the horn mount cylinder
  horn_mount_spacing = 10; // Space between the edge of the main body of the servo and the centre of the horn mount
  horn_main_height = 2; // Main body height only, not the rear section of the servo horn
  mock_servo = [40, 38, 19.5]; // Mock servo dimensions
  bracket = [7, 2.5, 19.5]; // Mock servo bracket dimensions
  gear_hole_bottom = 10 - 3.7 - 2; // Gear thickness - servo horn thickness - an extra 2mm

  color("white") translate([bracket.x + horn_mount_spacing, gear_hole_bottom + bracket_spacing + horn_mount_height + horn_main_height, mock_servo.z / 2]) rotate([90, 0, 0]) servo_gear(); 
  translate([bracket.x + horn_mount_spacing, bracket_spacing + horn_mount_height + horn_main_height, mock_servo.z / 2]) rotate([90, 0, 0]) mock_servo_horn();
  color("grey") mock_servo();
}

mock_servo_assembly();

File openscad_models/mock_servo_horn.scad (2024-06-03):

module mock_servo_horn(diameter=19.5, body_height=2, hole_diameter=1.5, rear_diameter=8.7, rear_height=1.7, centre_hollow_diameter=5.5) {
  total_height = body_height + rear_height;
  holes_height = total_height + 2;

    difference() {
      cylinder(d=diameter, h=body_height); // Main body
      translate([0, 0, -1]) cylinder(d=hole_diameter, h=holes_height); // Centre hole
    }

    difference() {
      translate([0, 0, body_height]) cylinder(d=rear_diameter, h=rear_height); // Raised rear section
      translate([0, 0, 0.2]) cylinder(d=centre_hollow_diameter, h=total_height + 1); // Centre hollow, 0.2 is best guess thickness of front of horn inside hollow
    }
}

mock_servo_horn();

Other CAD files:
openscad_models/servo_gear.scad
openscad_models/door_opener.scad
openscad_models/door_opener_cover.scad
openscad_models/gear_generator.scad
openscad_models/mounting_bracket.scad
openscad_models/pi_case.scad
openscad_models/reed_switch_mount.scad
openscad_models/screw_holes.scad
openscad_models/screw_post.scad
openscad_models/servo_post.scad
openscad_models/servo_rack.scad
openscad_models/switch_panel.scad

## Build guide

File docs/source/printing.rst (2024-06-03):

Printing the models
===================

Overview
--------
To start, customise and print the OpenSCAD models in ``/openscad_models`` as detailed below. Some of these are modules used in other files or libraries and you only need to print the models with a check mark in the print column. You should then assemble the models as per the instructions —

.. list-table::
   :header-rows: 1

   * - Filename
     - Description
     - Print?
     - Required filament
   * - ``door_opener.scad``
     - The door opener and cover.
     - ✓
     - 125g
   * - ``door_opener_cover.scad``
     - The door opener cover, used in the above file.
     - 
     - 
   * - ``gear_generator.scad``
     - Gear generator library by Leemon Baird, used to generate the rack and servo gear.
     - 
     - 
   * - ``mock_servo.scad``
     - A mock servo for modelling purposes, not intended to be printed.
     - 
     - 
   * - ``mock_servo_assembly.scad``
     - Fully assembled servo, including servo horn and gear, not intended to be printed.
     - 
     - 
   * - ``mock_servo_horn.scad``
     - A mock servo horn, not intended to be printed.
     - 
     - 
   * - ``mounting_bracket.scad``
     - Mounting bracket module, incorporated into the door opener, Pico case and switch panel.
     - 
     - 
   * - ``pi_case.scad``
     - Case and cover for the Raspberry Pi Pico.
     - ✓
     - 147g
   * - ``reed_switch_mount.scad``
     - Mounting block for reed switches to bring them in line with the door.
     - ✓
     - 12g
   * - ``screw_holes.scad``
     - Various sizes of screw holes used throughout the project.
     - 
     - 
   * - ``screw_post.scad``
     - Posts for brass M3 screw inserts, used in both the door opener and Pico case.
     - 
     - 
   * - ``servo_gear.scad``
     - Gear which is glued to a metal servo horn and engages with the rack.
     - ✓
     - 5g
   * - ``servo_post.scad``
     - Posts which the servo is screwed to, used in the door opener
     - 
     - 
   * - ``servo_rack.scad``
     - The rack which sits in the channel in the door opener and engages the servo gear, the far end is attached to the chicken coop door.
     - ✓
     - 54g (25% infill)
   * - ``switch_panel.scad``
     - A control panel to be attached to the front of your coop, has holes for a 7mm momentary switch and two 5mm LEDs.
     - ✓
     - 14g
   * - 
     - 
     - 
     - Total: 357g

Customisation and setup
-----------------------

General notes
^^^^^^^^^^^^^
* I printed these models using a Creality Ender 3 v2 printer, and the default settings for the rack in terms of sizing and cut position account for that.
* You'll obviously need OpenSCAD and a slicer, I personally use Prusaslicer. You'll also need to install the Belfry OpenSCAD library v2, installation instructions are on their `Github page. <https://github.com/BelfrySCAD/BOSL2>`_
* This door opener is built for the dimensions of my chicken coop, and as such will likely need customisation before it is suitable for yours. Generally speaking, I have implemented the most important customisation options as OpenSCAD parameters which can be changed directly within the OpenSCAD window, and direct changes to the code should be largely unnecessary. Once you've made your changes for each model, render the model and export it to .stl, ready for slicing.
* I'd suggest you use PETG to print your parts due to the increased tensile strength of that material, especially for the gear and rack but you can probably get away with using PLA if you really have to.
* In terms of required filament, the amounts quoted are at 15% infill unless otherwise noted. 

Door opener (\ ``door_opener.scad``\ )
^^^^^^^^^^^^^^^^^^^^^^^^^^^^^^^^^^^^^^
You'll need to change the door height (set to 20mm by default) so it is commensurate with the distance between where the door opener attaches to the coop and the top of your door, so that the bottom of the rack is in line with the top of the door and you can screw it into the door. To illustrate —

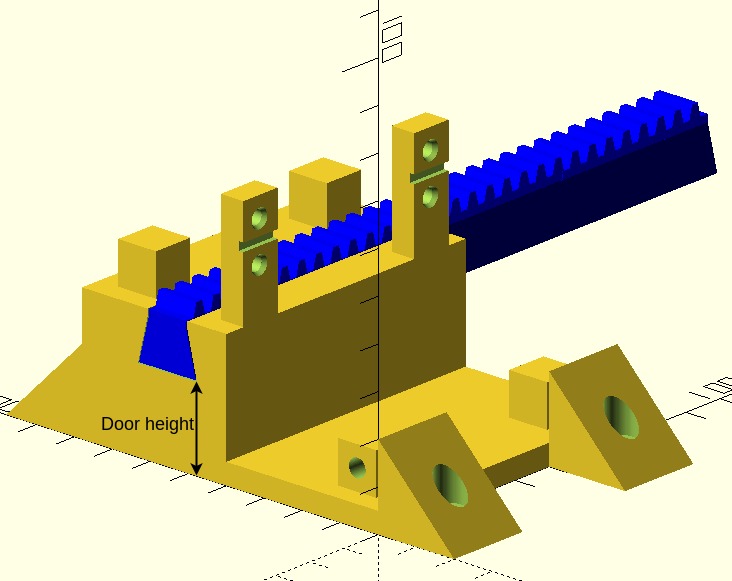
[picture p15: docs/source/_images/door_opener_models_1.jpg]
Door height illustration


Pi case (\ ``pi_case.scad``\ )
^^^^^^^^^^^^^^^^^^^^^^^^^^^^^^
For the cable entry hole in the base, the defaults for ``lip_diameter``\ , ``lip_height`` and ``inner_diameter`` are sized for a 30mm cable grommet I had lying around and may need to be tuned for something you buy (you could alternatively omit the grommet altogether). You should also ensure that supports are generated underneath the raised portions left and right of the mounting holes for the Pico in your slicer when printing.

Reed switch mounts (\ ``reed_switch_mount.scad``\ )
^^^^^^^^^^^^^^^^^^^^^^^^^^^^^^^^^^^^^^^^^^^^^^^^^^^
The reed switch mounts need to be of a suitable height so they are in line with the top of the door, so that when the reed switches are attached they line up with the magnets, which are attached to the door. Pictorially —

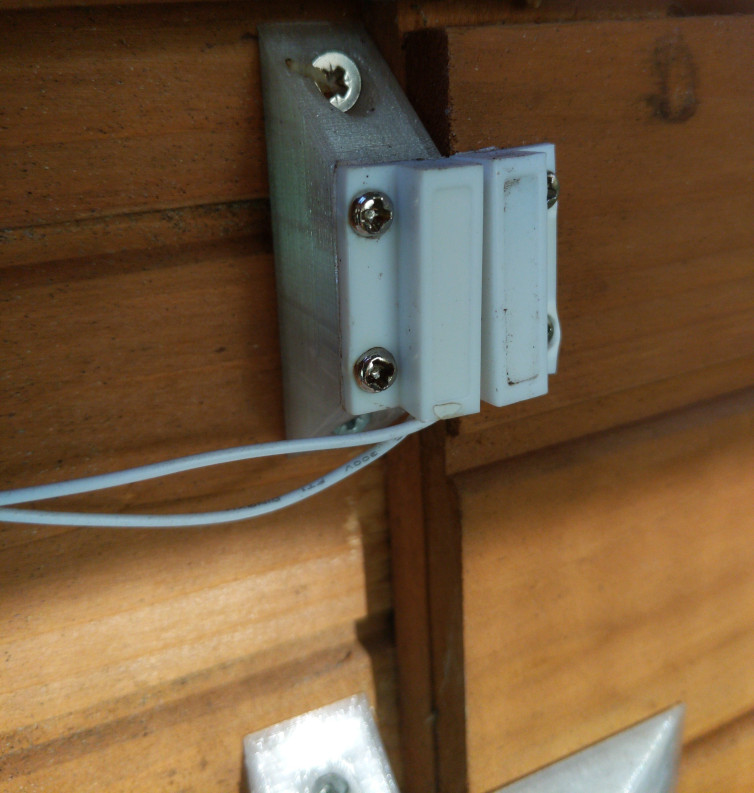
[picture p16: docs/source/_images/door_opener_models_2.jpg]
Reed switch illustration


In my case, I need two reed switch mounts of different heights as the point at which these are attached to my coop are at different heights relative to each other, but this may be unnecessary for your coop and you could potentially use two mounts of the same height.

Regardless, the customisation options allow for you to generate a tall or short reed switch mount as required, and you can customise both the "tall" and "short" heights if required. You should render and export two mounts as per your requirements.

Servo gear (\ ``servo_gear.scad``\ )
^^^^^^^^^^^^^^^^^^^^^^^^^^^^^^^^^^^^
There are no customisation options for this model, just render it and export to .stl. 

Servo rack (\ ``servo_rack.scad``\ )
^^^^^^^^^^^^^^^^^^^^^^^^^^^^^^^^^^^^
The servo rack provides the option of cutting it in two at a given point to allow a longer rack to be printed than would otherwise be possible on a typical printer bed. The default settings print a rack with a toothed portion of 312.5mm in length and will print on 220x220mm print bed when rotated 45 degrees around the Z axis (i.e. diagonally). Pictorially —

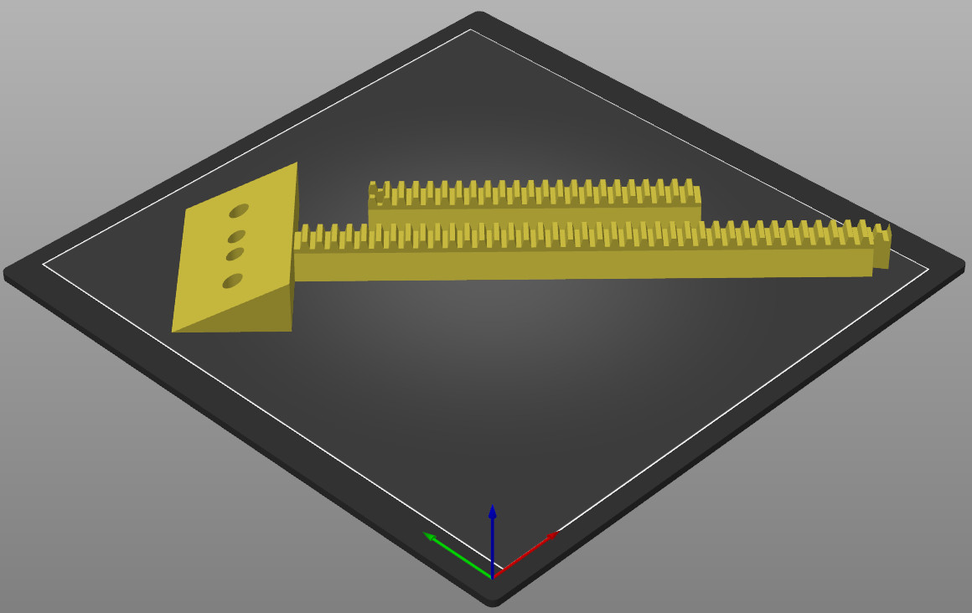
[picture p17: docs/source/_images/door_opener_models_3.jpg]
Rack printing illustration


Main options
~~~~~~~~~~~~
You need to set the minimum length of the rack to the distance between the edge of your coop door when closed, to the left hand edge of the door opener, i.e.

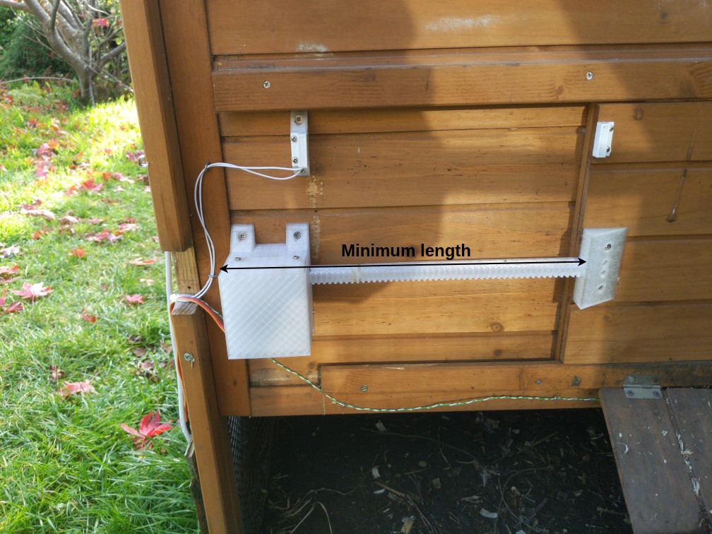
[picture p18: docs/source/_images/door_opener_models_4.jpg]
Minimum length illustration


Note that the *actual* generated length is 2.5mm longer than the length you specify due to tooth spacing.

You can also use the centre holes checkbox to determine whether holes in the centre are generated for 2.5 x 16mm screws (the screws included with my door), or whether all the holes are for 6x½ imperial screws. You probably want to untick this checkbox.

Cutting options
~~~~~~~~~~~~~~~
You can enable or disable cutting the rack at all using the ``dovetail rack`` checkbox,  the options that follow are only applicable when this is checked.

``cut length`` determines the point at which the right hand side of the rack is cut, and includes the length of the bracket portion (40mm). I'd suggest you make this as long as possible as will fit on your print bed as to minimise the length of the joined portion. 

``cut x``\ and ``cut y`` determine the position of the cut portion (left hand side) of the rack, you might need to adjust this so that you can fit the entire model on your print bed.  

``$slop`` determines the tolerance included for the dovetail joint, this is set to 0.2mm for my printer (a Creality Ender 3 v2) by default. The BOSL2 library github wiki has a `calibration print <https://github.com/BelfrySCAD/BOSL2/wiki/constants.scad#constant-slop>`_ that you can use to determine the correct value if you don't want to guess.

Switch panel (\ ``switch_panel.scad``\ )
^^^^^^^^^^^^^^^^^^^^^^^^^^^^^^^^^^^^^^^^
There are no customisation options for this model. Be sure to print with supports in the interior portion of the switch panel, where the LEDs and momentary switch are mounted.

Assembly
--------
Once you've customised and printed all the parts listed above, you'll need to do the following assembly so that you're ready to wire everything up and mount the project to your coop. You may want to refer back to :doc:`video and images <video>` to get a general feel for how everything fits together —

Servo rack
^^^^^^^^^^
Glue the two parts of the rack together at the dovetail joint and try as best you can to ensure that the bottom is flat at the join. You'll probably find that the two sides don't line up exactly when the glue is dry, and you should sand the join to prevent the rod from hitching at the join when the door opens and closes.

Servo gear
^^^^^^^^^^
Glue the flat side of the aluminium servo horn into the centre of the servo gear. Once dry, attach to the hub of the servo motor with the M3 x 8 screw.

Door opener
^^^^^^^^^^^
Place the four brass M3 screw inserts into the posts on the front and rear of the base of the door opener, and melt into place using a soldering iron. Lubricate the channel for the door opening rod with a small amount of silicone grease. Mount the servo motor on the mounting posts using the four M3 x 12 screws and nuts — looking at the servo from the channel side, the gear should be on the right side. Insert the rack into the left hand side of the channel so it is touching the gear and will be engaged by the gear when it moves anti-clockwise. Run the wires for the servo through the hole in the cover, and attach the cover to the base with the four M3 x 10 screws.

Pi case
^^^^^^^
Place the four brass M3 screw inserts into the posts at the top and the holes in the bottom wall of the pi case, and melt into place using a soldering iron. Place the four brass M2 screw inserts into the four holes in the centre of the case, and also melt those into place. Solder the two 20 pin headers onto the Pico so that the longest portion of the header is on the top (short section is soldered to the board on the underside). Screw the Pico into place in the centre of the case using the four M2 x 6 screws so that the micro USB connector is facing the hole in the wall. Push the 30mm cable grommet into place, if using. Mount the female DC connector on the left raised portion in the base using cable ties, and do the same with the relay module on the right raised portion. You can now do a test fit of the cover to ensure it fits and the cable ties don't cause problems — the ones I used were relatively thin.

Reed switch mounts
^^^^^^^^^^^^^^^^^^
Mount the reed switches to the reed switch mounts using the included 2.5 x 10mm screws.

Switch panel
^^^^^^^^^^^^
Looking at the switch panel from the front with the hood portion at the top, glue the green LED into the left hole and the red LED into the centre hole. Once dry, screw the 7mm momentary switch into place into the right hand hole such that the nut is on the front side of the panel.

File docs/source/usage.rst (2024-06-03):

Usage
=====

Assuming you've deployed and configured the Pico at this point it should be ready to boot standalone, but I'd suggest at least initially you start it manually via running ``main.py`` in Thonny so you can view debug output in the console.

Starting in button operation mode
---------------------------------
As previously mentioned, if you want to start without network functionality you need to delete ``/lib/dooropenerpico/credentials.conf`` after which the door opener can be operated by use of the control panel switch. On boot, the red and green LEDs on the control panel flash alternately twice to indicate that the Pico has successfully started.

Starting in network mode
------------------------
Network mode is the default mode the Pico starts in, assuming the presence of ``/lib/dooropenerpico/credentials.conf``. A successful boot looks like the following —

* The onboard LED blinks slowly to indicate that the Pico is attempting to connect to Wifi.
* The onboard LED blinks more quickly to indicate that the Pico is attempting to connect to the MQTT broker.
* The onboard LED goes solid to indicate that a connection has been established.
* The red and green LEDs on the control panel flash alternately twice to indicate that the Pico has successfully started.

At this point the Pico is ready to accept commands via the button on the control panel or via MQTT messages.

.. _console-output:

In the console, a successful boot looks like this —

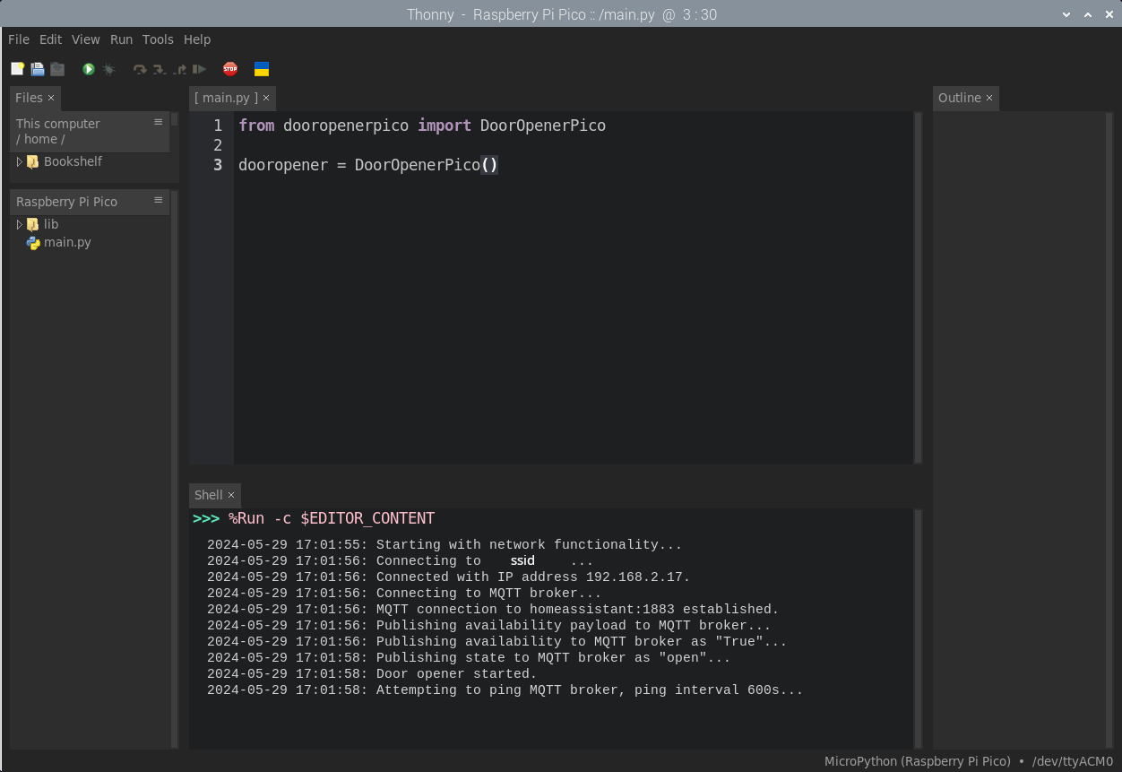
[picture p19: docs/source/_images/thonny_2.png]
Successful Pico startup in Thonny


Starting in web server mode
---------------------------
You can start the Pico with a web server for debugging purposes by holding the switch on the control panel when the Pico starts (when power is applied, or when you start ``main.py`` manually). You can verify that the Pico started in web server mode from the console —

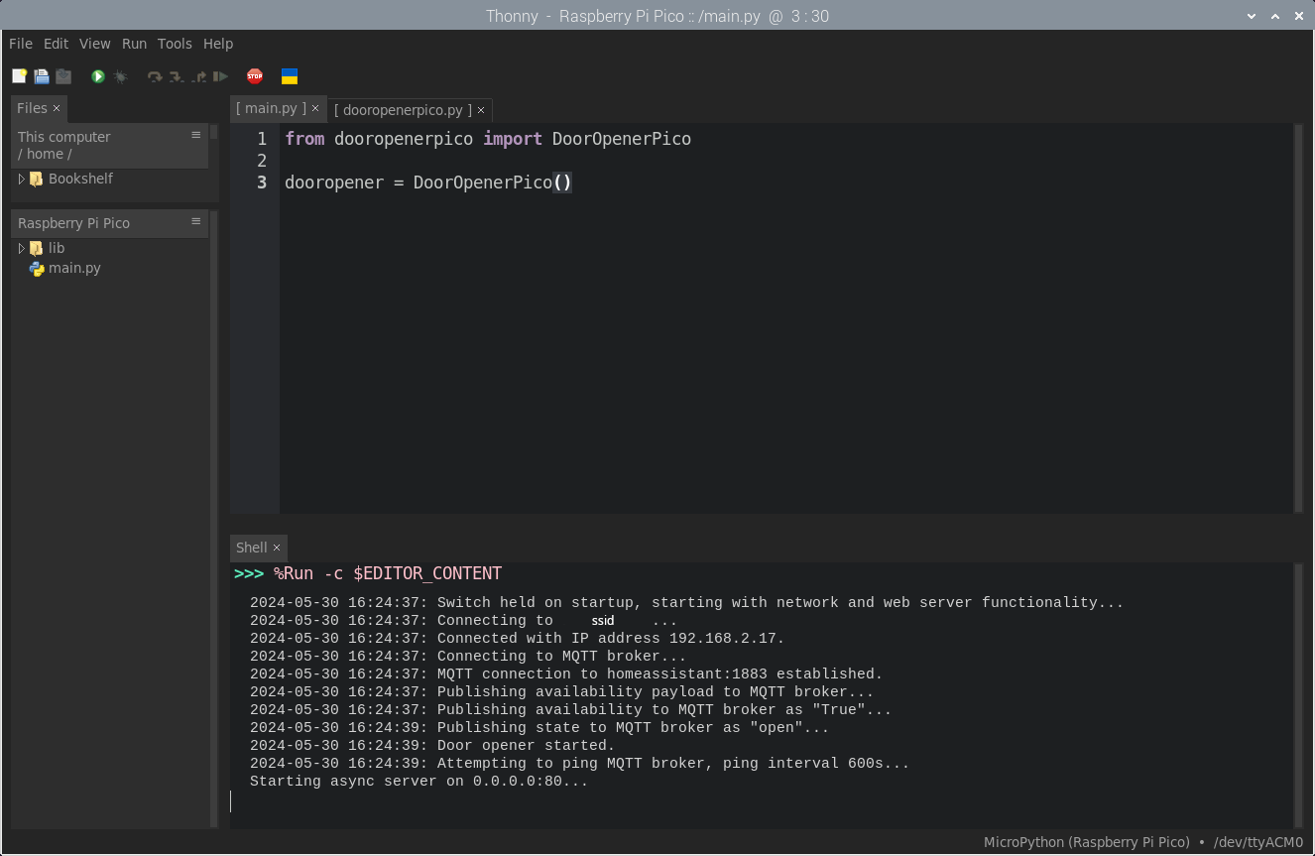
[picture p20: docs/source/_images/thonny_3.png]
Console indicating web server mode


.. warning::
   No security measures are implemented in the web server and this mode is intended for setup and debugging rather than permanent use.

.. _web-server:

If you then navigate to the IP address of the Pico in your web browser, you'll be presented with the following (mobile friendly) page —

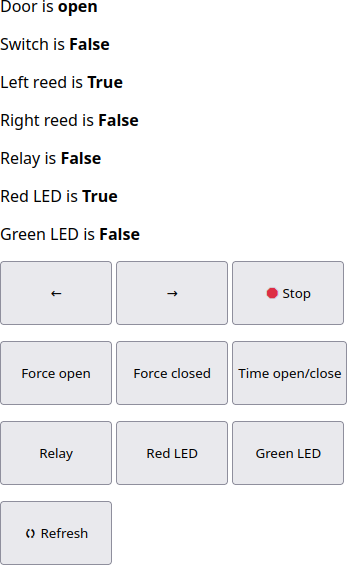
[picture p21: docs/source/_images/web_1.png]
Door opener web UI


The function of the buttons should be fairly self explanatory but there are some things of note —

* The left and right arrows move the servo in those directions. You can also use the left and right keys on your keyboard if you're on a desktop computer. The speed for these actions can be set in ``config.conf`` as detailed in the :ref:`configuration options<configuration-options>` section.
* The stop button stops the servo, but this will not interrupt the current action (i.e. if the door is opening or closing) and is intended for use so that you can set the trim pot appropriately to the stop position on the servo.
* Force open and closed function as named.

.. warning:: 
   Force open and closed don't check the state of the door before attempting to actuate, so be careful you pick the correct button or you could damage the servo.

.. _time-open-close:
   
* Time open/close will time how long the door takes to actuate, see below. This is useful for determining the appropriate timeout setting in ``config.conf``, see the :ref:`configuration options <configuration-options>` section for more details.

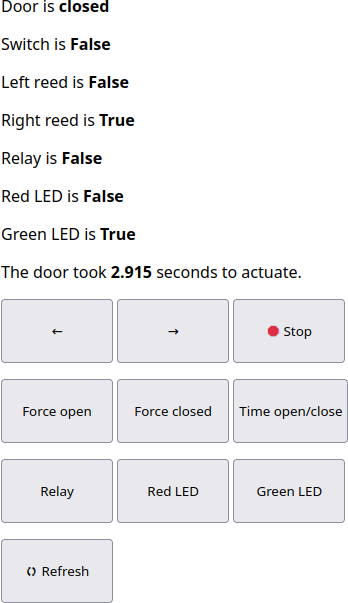
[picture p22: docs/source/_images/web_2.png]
Timing door actuation in the web UI


* Relay, Red LED and Green LED toggle the state of those devices, useful for testing your wiring.
* Refresh forces the page to retrieve the current state of the door opener.

LED meanings
------------

The various LEDs on the Pico and control panel are all used to indicate status, as such —

**Pico LED**

* Flashing slowly means the Pico is attempting to connect to wifi.
* Flashing quickly means the Pico is attempting to connect to the MQTT broker.
* Solid illumination means that a connection to both wifi and the MQTT broker has been established.

**Green LED**

* Pulsing means the door is closing.
* Solid illumination means the door is closed.

**Red LED**

* Pulsing means the door is opening.
* Solid illumination means the door is open.
* Flashing means the door is in the error state, and the last action was aborted. This could be because the door was already in the state requested (e.g. recieved an MQTT open message when the door was already open) or because the door opener couldn't determine whether it was open or closed.

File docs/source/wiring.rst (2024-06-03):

.. include:: global.rst

Wiring and assembly
===================

General guidelines
-------------------
It is difficult to give specific instructions with regards to how to mount and wire everything as your chicken coop is likely slightly different to mine, so I'm only going to provide general guidelines in this section. With that in mind —

* You might want to try initially wiring everything indoors to ensure you have the basic functionality working, but there's obviously only so far you can go without having the parts actually mounted to your coop. At minimum you'll probably want to copy the code to the Pico, but as every setup is likely to be slightly different I'll leave it to your judgement as to when to actually mount everything.
* Refer to the :doc:`video and images <video>` section for an idea of how everything fits together once mounted. The Pico case also has mounting points for screws in case you need them, but mine is in a plastic box around the side of the coop and is not mounted. You'll need to attach —

  * The control panel to a suitable position where you can access the switch easily.
  * The reed switch mounts such that they mate with the magnets mounted either side of the door, in both open and closed positions.
  * The door opener so the centre of the rack is aligned with the centre of the door, and can fully retract and open the door.
  * The rack bracket with the centre of the door, so the back of the bracket is aligned with the edge of the door. 

* You'll use the female dupont cables to connect to the Pico headers, you'll generally need to splice these with the suggested wires for components that are some distance away from the Pico, like the reed switches, control panel and so on.
* On the control panel, you should connect the negative side of the switch and cathode (negative) sides of the red and green LEDs together so they can be connected to a single ground on the Pico side. If you're using a Cat5 cable as suggested, the easiest way to do this is to use individual wires on the control panel side and solder them all together at the far end before splicing all three wires to a single black female dupont cable.
* You'll need to solder a 330Ω resistor inline with the anode (positive) side of both the green and red LEDs, I tacked these between the far end of the cables and put heatshrink over them.

Wiring diagram
--------------
You need to wire all the electronic components as per the following diagram —

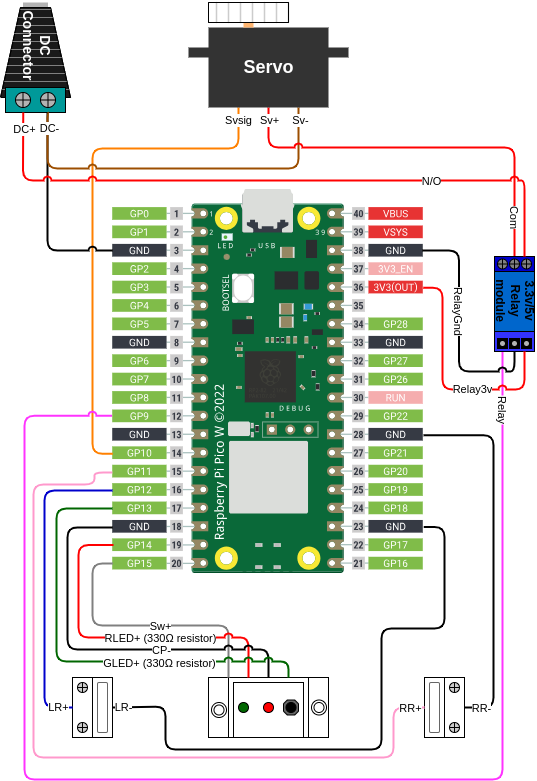
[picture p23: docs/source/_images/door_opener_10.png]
Door opener pico wiring diagram


In tabular form (this table is laid out in the same manner as the diagram i.e. Micro USB connector at the top) —

.. list-table::
   :header-rows: 1
   :align: left

   * - GPIO pin
     - Name
     - 
     - Name
   * - 
     - /
     - 
     - /
   * - 
     - /
     - 
     - /
   * - /
     - DC- / Servo -
     - 
     - Relay -
   * - 
     - /
     - 
     - /
   * - 
     - /
     - 
     - Relay 3v
   * - 
     - /
     - 
     - /
   * - 
     - /
     - 
     - /
   * - 
     - /
     - 
     - /
   * - 
     - /
     - 
     - /
   * - 
     - /
     - 
     - /
   * - 
     - /
     - 
     - /
   * - 9
     - Relay signal
     - 
     - /
   * - /
     - /
     - 
     - Right reed -
   * - 10
     - Servo signal
     - 
     - /
   * - 11
     - Right reed +
     - 
     - /
   * - 12
     - Left reed +
     - 
     - /
   * - 13
     - Green LED +
     - 
     - /
   * - /
     - Control panel -
     - 
     - Left reed -
   * - 14
     - Red LED +
     - 
     - /
   * - 15
     - Switch +
     - 
     - /

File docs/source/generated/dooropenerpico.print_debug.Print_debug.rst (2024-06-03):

Print\_debug
============

.. currentmodule:: dooropenerpico.print_debug

.. autoclass:: Print_debug

   .. automethod:: __init__

   .. rubric:: Methods

   .. autosummary::
   
      ~Print_debug.__init__
      ~Print_debug.print_debug

   .. rubric:: Attributes

   .. autosummary::
   
      ~Print_debug.print_timestamps
      ~Print_debug.rtc

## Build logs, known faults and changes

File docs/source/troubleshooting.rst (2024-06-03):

Troubleshooting and known issues
================================

General suggestions
-------------------

* A laptop or another machine running Thonny is essential for debugging issues when setting up the door opener. I personally have a Raspberry Pi Zero 2W running VNC that I can connect to and check the console output.
* Wireless signal strength was a fairly consistent source of issues for me early on until I set up an additional wireless access point in a mesh configuration. The MQTT client library used is to some extent resilient to connection issues and attempts to maintain the connection but having a strong signal to start with will save you some frustration.

Known issues
------------

* LED pulsing on open/close is deliberately disabled when the door opener is running in web server mode as this results in a crash due to the limited stack size of the Pico. I've raised other issues with the underlying ``picozero`` library used in the project that haven't been addressed, so I'm unsure if this can be rectified.
* I feel this project is pushing at the limits of the capabilities of the Pico in terms of resources, being implemented in a polymorphic object-oriented manner and making extensive use of third party libraries. I had to cross-compile the libraries into native bytecode to allow everything to fit into memory, and the project would probably benefit from a rewrite in a lower level language such as C (no plans currently to do that).
